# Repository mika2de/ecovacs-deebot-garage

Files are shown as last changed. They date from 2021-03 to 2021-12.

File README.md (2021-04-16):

# Automated robot vacuum cleaner garage

## Description

The robot controlls it all! 100% automation, no manual interactions, invisible installation.

The robot leaves the charging station and operates a mechanical switch that turns on the power. The software opens the door immediately, waits 30 sec to give the robot enough time to leave the garage and then closes the door.

On return it sends an event to the manufactor's server. The software listens to this event, sets the garage into homecoming mode, opens the door and waits for the robot to arrive. A thin force sensing resistor, placed a few centimeteres in front of the charging station, notices when the robot overruns it. That gives the signal to close the garage door right before the power is switched off again.

If the robot didn't return within 5 minutes it is assumed to be trapped and the door gets lowered again. Remove the barriers, say `hey google, return my robot to charging dock` and both robot and garage door execute the homecoming command.

***

## Videos

Robot vacuum cleaner leaves the docking station. 

Automated robot vacuum cleaner garage - start cleaning (https://www.youtube.com/watch?v=2y_Sdoj8P9I "Automated robot vacuum cleaner garage - start cleaning")

The robot returns to the charging station. The ESP received the homecoming event, opened the door and waits for the robot to run over the force resistance sensor.

Automated robot vacuum cleaner garage - returning home (https://www.youtube.com/watch?v=6Qcx_HnqS7c "Automated robot vacuum cleaner garage - returning home")

The kitchen skirting board is heavy, a regular nema 17 cannot lift or hold it. Thus it needs a gearing mechanism. Lucky you if you have a 3D printer at home.

Automated robot vacuum cleaner garage - returning home (https://www.youtube.com/watch?v=Ibu8yQTSDAc "Automated robot vacuum cleaner garage - returning home")

***

## How it works

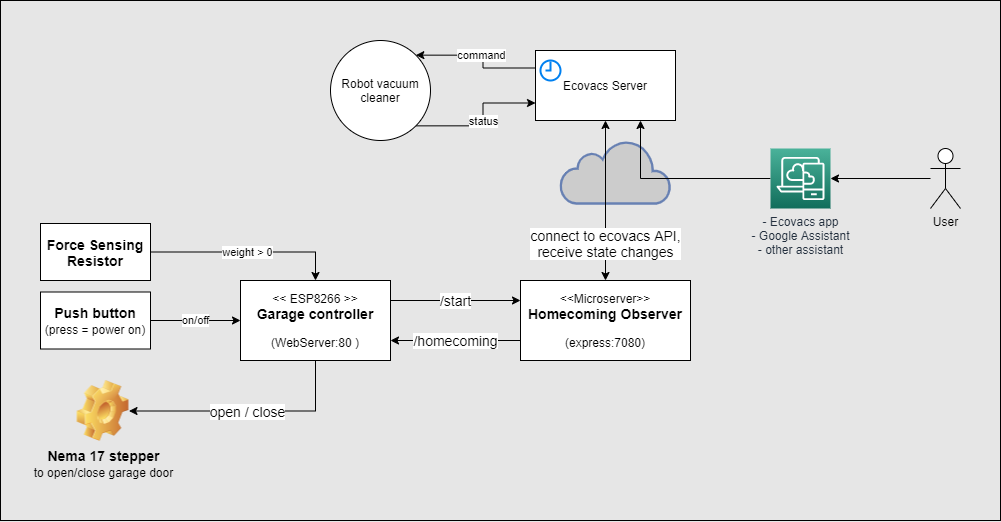
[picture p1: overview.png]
overview


The ESP8266 operates a nema 17 stepper motor that lifts the kitchen skirting board up and down. As long as the robot is in parking postion, one of the robot's wheels stand on an inverted push button so the ESP is powered off. The power is turned on when the robot starts leaving the docking station. On startup the controller executes the following startup routine:

```C++
void setup(){
  Serial.begin(9600);

  // stepper pins
  pinMode(enablePin, OUTPUT);
  pinMode(stepPin, OUTPUT);
  pinMode(dirPin, OUTPUT);

  // force resistance pin
  pinMode(frsPin, INPUT);

  openDoorWaitAndClose(); // function waits 30 sec before closing the door again
 
  // connect to home WiFi
  WiFi.mode(WIFI_STA);
  WiFi.begin(ssid, password);
  Serial.print("Attempting to connect to WPA ");
  Serial.println(ssid);
  if (WiFi.waitForConnectResult() != WL_CONNECTED) {
    Serial.println("WiFi failed!");
    return;
  }
  Serial.println("connected");
  Serial.println(WiFi.localIP());

  // register API endpoints on ESP8266WebServer
  server.on("/open", handleOpenDoor); // for test usage
  server.on("/close", handleCloseDoor); // for test usage
  server.on("/homecoming", handleHomecoming); // for use by nodejs server
  server.onNotFound(handleNotFound); 
  server.begin();
  Serial.println("HTTP server started");

  // send signal to nodejs server
  wakeupBackendService();
}
```
The nodejs server opens a connection to the Ecovacs REST API and starts to listens for inbound status notification events. If the "returning" event is received, the program forwards the event via http to the ESP8266WebServer.

```js
const observe = async () => {
    if (vacbot !== undefined) {
        console.log('Already observing')
        return
    }
    console.log('Start observing')

    const connectStatus = await api.connect(username, passwordHash)
    const devices = await api.devices()
    let vacuum = devices[0];
    vacbot = api.getVacBot(api.uid, EcoVacsAPI.REALM, api.resource, api.user_access_token, vacuum, continent)

    vacbot.on('ready', async (event) => {
        console.log('Vacbot ready')

        vacbot.on('CleanReport', async (state) => {
            console.log('CleanReport: ' + state)

            if (state === 'returning') {
                disconnect()
                vacbot = undefined

                console.log('Try open garage door')
                var response = await openGarage()
                console.log('Garage door opens...')

                let i = 0
                while (response !== 200 && i < 5) {
                    i++;
                    console.log(`Error ${response}, retry open garage door #${i}`)
                    response = await openGarage()
                    await sleep(500)
                }
            }
        })
    })

    process.on('SIGINT', function () {
        console.log("\nGracefully shutting down from SIGINT (Ctrl+C)")
        disconnect()
        process.exit()
    });

    function disconnect() {
        try {
            vacbot.disconnect();
        } catch (e) {
            console.log('Failure disconnecting: ', e.message)
        }
    }
}
```

The ESP is now set into homecoming mode. The homecoming function waits for the robot to run over the force sensing resistor, that is placed right in front of charging station, and closes the door in the final moment before the system is powered off again.

```C++
void homecoming(){
  openDoor();
  do {
    frsValue = analogRead(frsPin);
    delay(500);
  } while (frsValue == 0); // wait for force resistance sensor signal, the quickly close the door before the power is turned off
  closeDoor();
}
```

***

## Build instructions

### NodeMCU, motor and force sensitive resistor wiring

My circuit is run by a single 12V 5A power supply. A  L298N H-Bridge that I had in spare converts 12V in 5V and provides this as input to the ESP8266. This allows me to easily switch on/off the ESP8266 and the stepper driver by a push button. 

In my first experiments I used the L298N to operate the Nema 17 stepper. That wasn't a good idea. I burned my ESP8266 when I performed a physical load test  to figure out how much kilogram the motor (and driver) is able to lift and hold. So I read a bit about stepper drivers other guys use and gave it a try with the A9488 stepper driver. Even under stress it works like a charm, in the worst case the stepper overruns a step.

The A9488 has a on-board potentiometer that one can use to adjust voltage for the motor. Default setting was already good but not sufficient, in my case a quater turn in clockwise direction gave the motor enough power to lift my 1 kg kitchen skirting board.

Don't forget the electrolytic capacitor (100 µF) to protect the stepper driver from spikes.

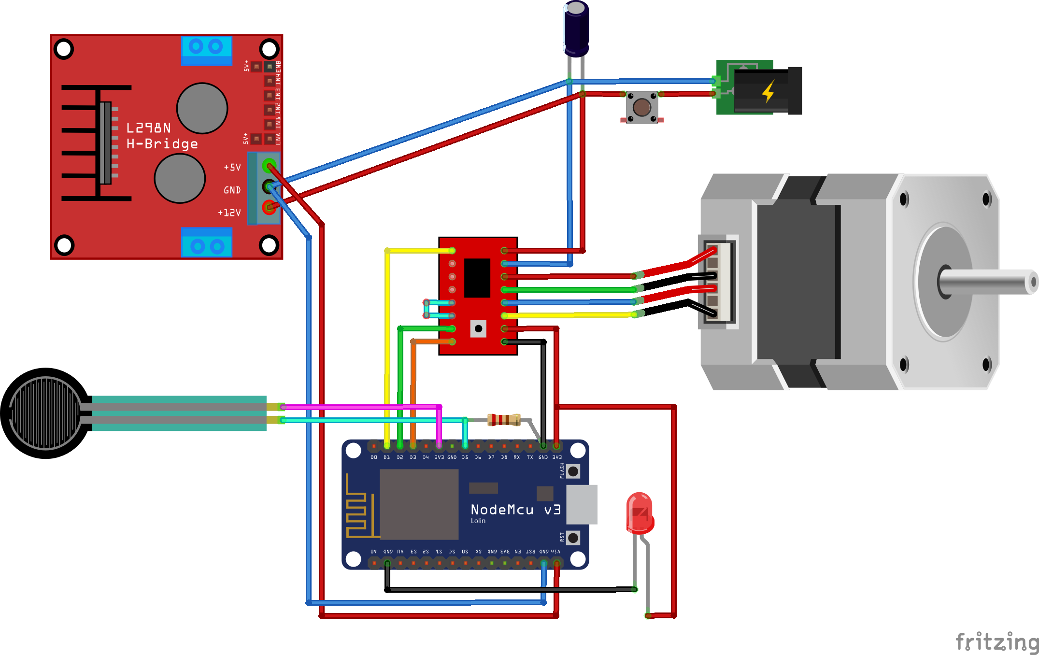
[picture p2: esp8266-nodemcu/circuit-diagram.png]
circuit diagram


### 3D print the reduction gear

For this reduction gear design I finally did my first steps with OpenSCAD. To get accurate gears I used the MCAD/involute_gears.scad library. For my [previous designs](https://www.thingiverse.com/mika2de/designs) I used FreeCAD which was sort of okish for me, but now that I switched to OpenSCAD there is no going back. The reduction gear source file is available in folder cad-models, modify according to your needs. In addition you might find https://geargenerator.com/ helpful, too. 

Reduction gear in OpenSCAD

### Prepare the kitchen skirting board

Check the following image on how to install the hings on your kitchen skirting board. If the hing is not centered like in the middle picture, your skirting board won't hang in a 90° angle from your cupboard. However, when the hinge is centered and you place your skirting board not directly at the front of cupboard but a few centimeters back, you need a pad to open the garage door completely without being blocked by the bottom of the cupboard. 

How to mount the skirting board

Depending on your hinge, you can customize yourself the pad with just a few lines of OpenSCAD code:

```C++
difference() {
    cube([42,11,7]);
    translate([1,0,-0.1]) cube([40,10,1.2]);
    translate([8,5,0]) cylinder(h=20,r=1.5,$fn=20);
    translate([34,5,0]) cylinder(h=20,r=1.5,$fn=20);
}
```

### Run homecoming observer in background

I've a HP microserver running at home, which I reused to host my tiny nodejs homecoming observer program. I installed it in a unix VM and configured it to run after VM startup. 

### Install hardware

Mount the reduction gear to a e.g. wood construction of your choice. If you don't have much space like me, try to position the stepper motor higher at a height that allows the robot vacuum cleaner to drive under it. This gives the robot a bit more space to move. 

parking position image 1

The force sensitive resistor's purpose is to give a signal to the ESP8266 to close the door when the robot is back in the garage. Since the circuit will be powered off as soon as the robot wheel stands on the inverted push button you need to place the FSR needs to be placed a few centimeters in front of the push button. This also depends on the speed of your robot. The slower the robot move towards the charging station, the closer you can put the FSR to the push button. If you put it too close to the button, it could happen that the ESP has not enough time to close the door before it is powered off.

parking position image 1

parking position image 1

## More 

See project log on https://hackaday.io/project/178993-space-saving-automated-robot-vacuum-cleaner-garage

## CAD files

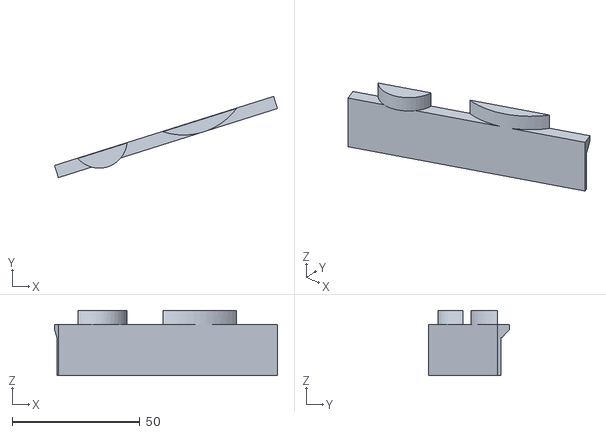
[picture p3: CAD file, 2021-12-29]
cad-models/v2/mount-of-giant-motor-mount.stl
87.3 x 31.8 x 25.5

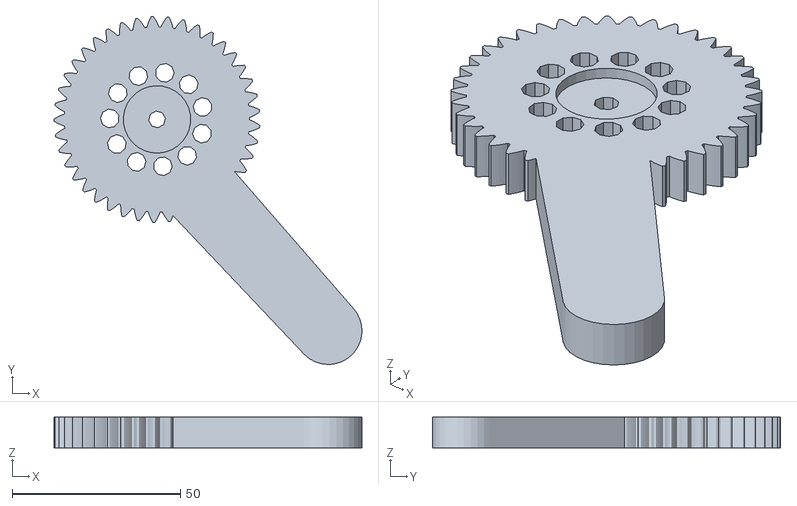
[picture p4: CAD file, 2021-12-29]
cad-models/v2/lift-door-arm.stl
91.4 x 103.3 x 9.20

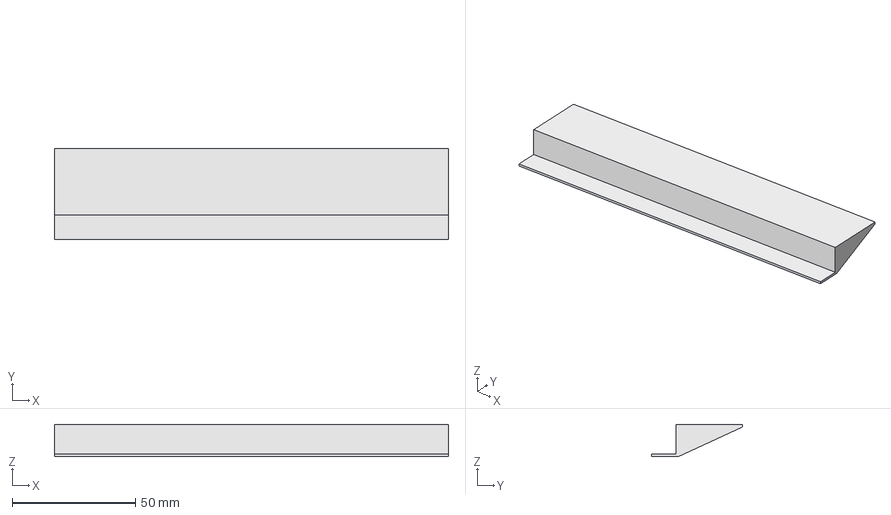
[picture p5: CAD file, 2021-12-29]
cad-models/v2/ramp.FCStd
160.0 x 37.0 x 13.0 mm

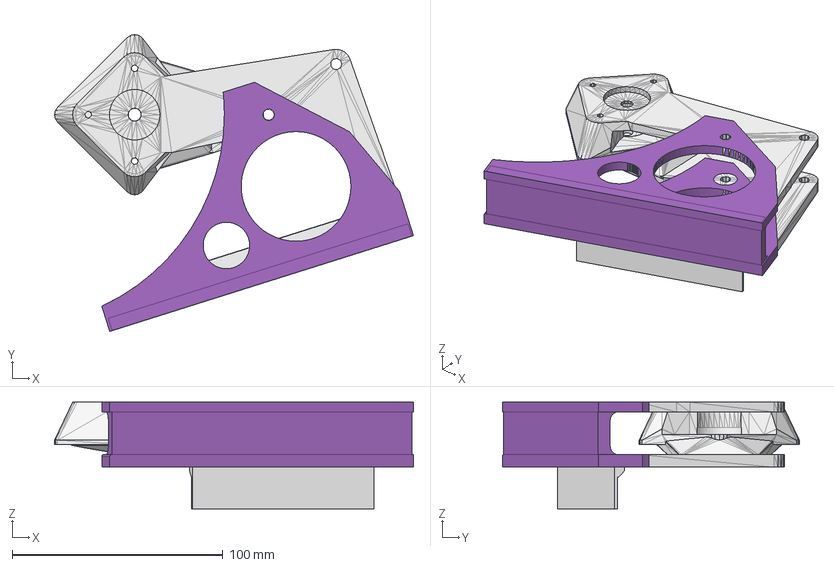
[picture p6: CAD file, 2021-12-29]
cad-models/v2/giant-motor-mount.FCStd
170.2 x 140.7 x 50.5 mm
Würfel003

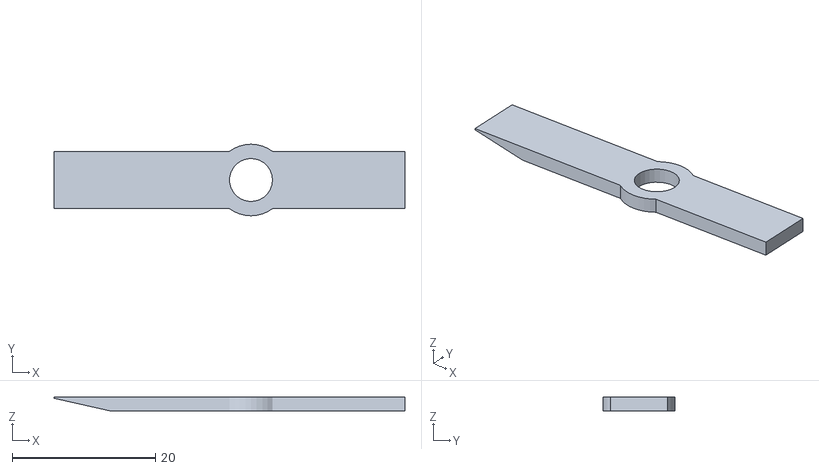
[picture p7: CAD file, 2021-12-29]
cad-models/v2/small-gear-mount.stl
49.0 x 10.0 x 2.00

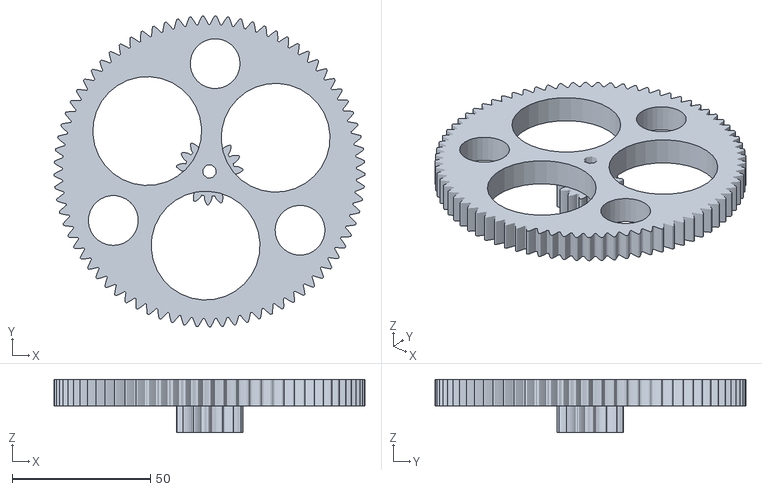
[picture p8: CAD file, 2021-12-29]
cad-models/v2/double-gear.stl
112.3 x 112.3 x 19.2

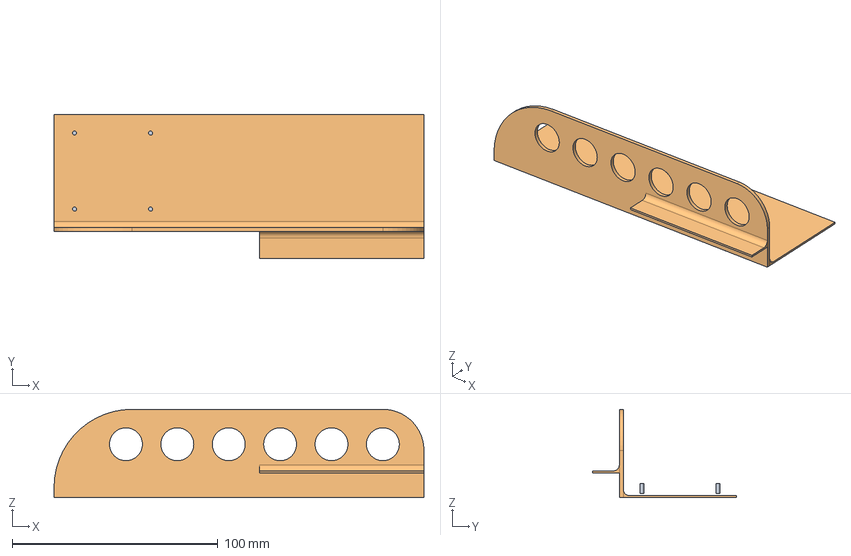
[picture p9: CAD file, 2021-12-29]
cad-models/v2/circuit-plate.FCStd
180.0 x 70.0 x 43.0 mm

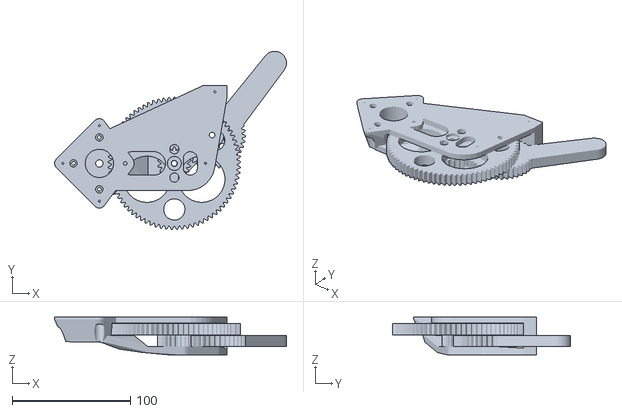
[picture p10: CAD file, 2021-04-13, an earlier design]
cad-models/v1/garage-door/assembling.stl
196.5 x 151.1 x 31.8

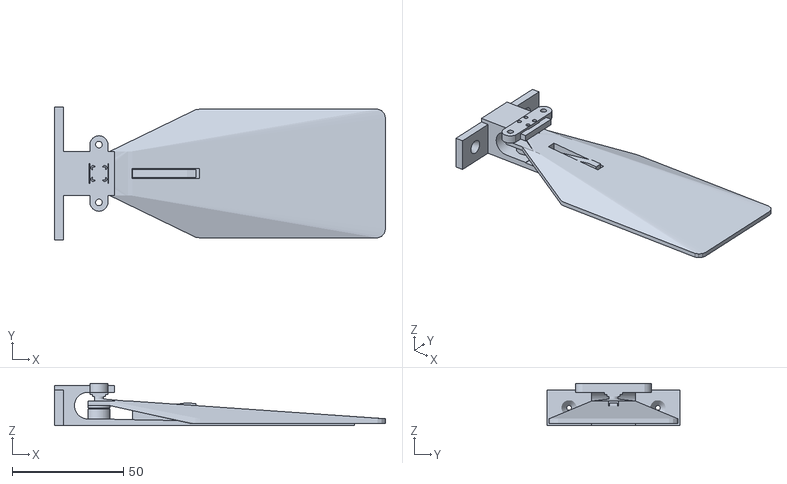
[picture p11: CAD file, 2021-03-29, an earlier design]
cad-models/v1/docking-switch/assembling.stl
149.0 x 60.0 x 19.0

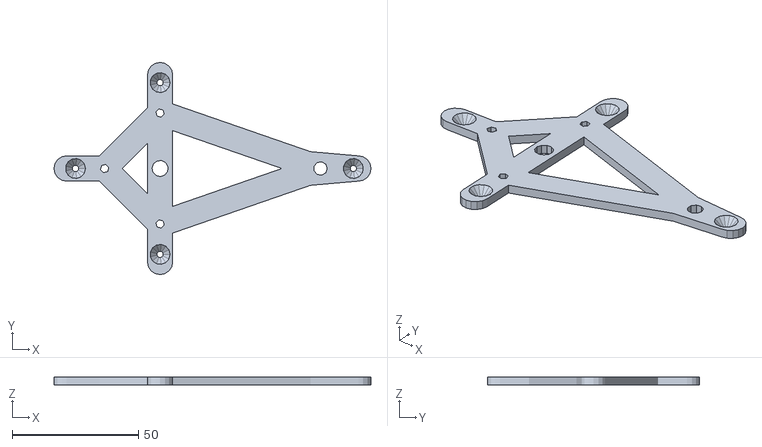
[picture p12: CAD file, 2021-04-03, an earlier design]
cad-models/v1/docking-switch/wall-mount.stl
125.5 x 84.0 x 3.00

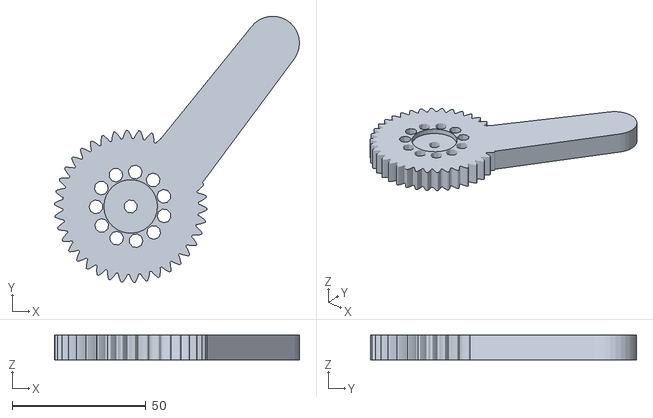
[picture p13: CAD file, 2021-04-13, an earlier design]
cad-models/v1/garage-door/gear-with-arm.stl
91.4 x 99.4 x 9.20

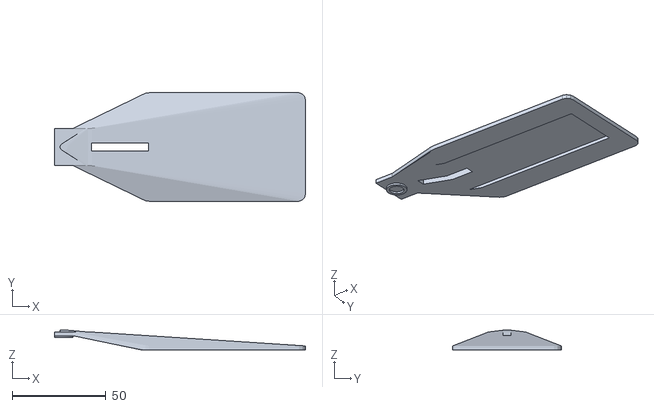
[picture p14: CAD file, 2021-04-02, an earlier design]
cad-models/v1/docking-switch/base-plate.stl
134.0 x 57.9 x 10.5

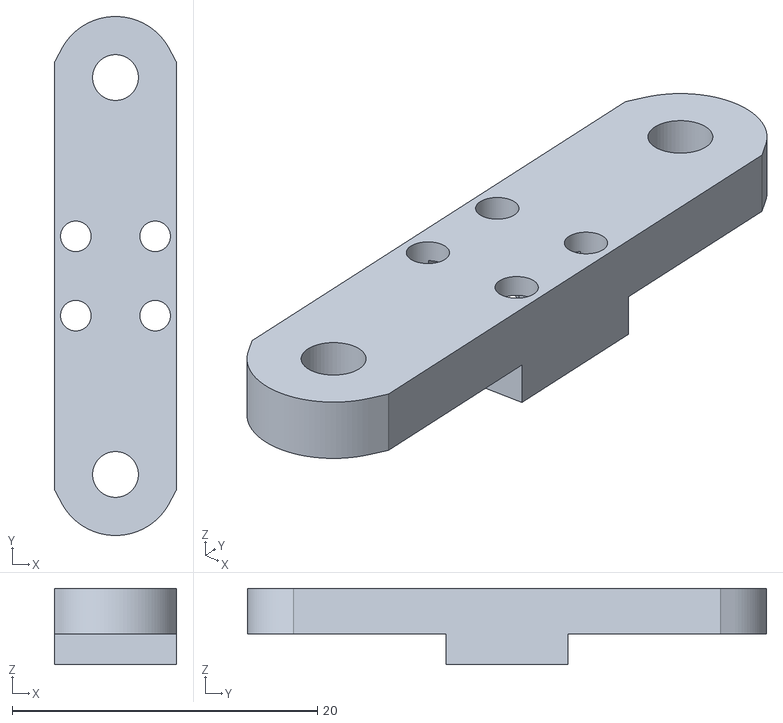
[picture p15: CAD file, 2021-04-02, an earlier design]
cad-models/v1/docking-switch/switch-mount.stl
8.00 x 34.0 x 5.00

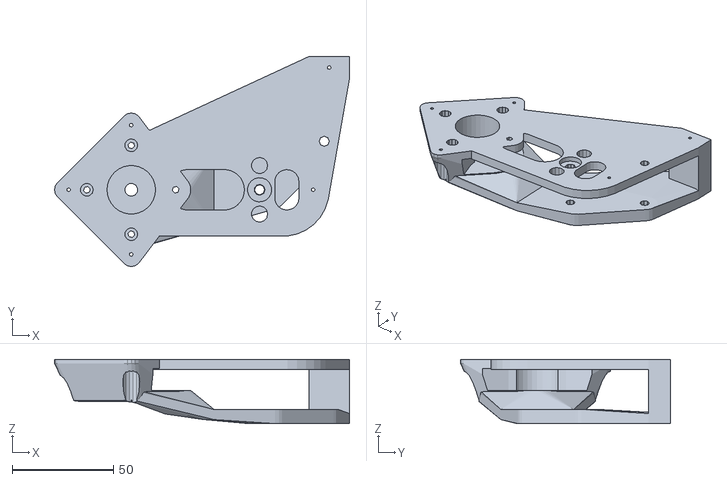
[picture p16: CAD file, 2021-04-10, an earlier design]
cad-models/v1/garage-door/motor-mount.stl
146.0 x 104.0 x 31.8

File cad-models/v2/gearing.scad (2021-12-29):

// DRAFT
// Quick'n dirty cad file used to export the unfinished giantMount.stl which I used as input for FreeCad to finally finish it.

use <MCAD/involute_gears.scad>
include <MCAD/stepper.scad>

tol_x = .2;
tol_z = .4;
gear_thickness=10;

module newGear(teeth, gear_thickness, circle) {
    gear(
        number_of_teeth=teeth,
        circular_pitch=256,
        twist=0,
        rim_width=2,
        rim_thickness=gear_thickness-tol_z,
        hub_diameter=5,
        hub_thickness=gear_thickness-tol_z,
        gear_thickness=gear_thickness-tol_z,
        circles=circle,
        bore_diameter=5
    ); 
}


module liftDoorArm() {
    difference() {
        translate([32,24,-10+tol_z]) rotate([0,0,17]) newGear(41,10-tol_z,11);
        translate([32,24,-3+tol_z]) cylinder(10-tol_z, r=10);
    }
    hull() {
        intersection() {
            translate([32,24,-10+tol_z]) rotate([0,0,-2.5]) newGear(38,10-tol_z,5);
            translate([55,45,-10+tol_z]) cylinder(10-tol_z, r=13);
        }
        translate([85,85,-10+tol_z]) cylinder(10-2*tol_z, r=10);
    }

}

module doubeGear() {
    color("LightBlue") difference() {
        newGear(77,10,3);
        for(n = [1 : 3])
                rotate([0, 0, 60 + n * 120])
        {
            translate([39,0,0])
            cylinder(50, r=9);
        }
    }
    
    translate([0,0,-10+tol_z]) color("LightYellow") newGear(15,10,7);
    //rotate([0,0,-90]) liftDoorArm();

}

module small_gear(teeth) {
    color([0,0,1]) translate([-2.5,1.9,0]) cube([5,2,15-tol_z]);
    gear(
        number_of_teeth=teeth,
        circular_pitch=256,
        twist=0,
        rim_width=2,
        rim_thickness=gear_thickness,
        hub_diameter=10,
        hub_thickness=15-tol_z,
        bore_diameter=5+4*tol_x,
        gear_thickness=gear_thickness-1,
        circles=5
    );
}

module nema() {
    motor(Nema17, NemaShort);
}

module nema17_hole(depth=10) {
    linear_extrude(depth) minkowski() {
        circle(6);
        square([31.04, 31.04], true);
    }
    translate([0, 0, -depth])
    cylinder(depth+1, r=3+tol_x);
    for (i = [0:3]) {
        rotate([0, 0, i*90])
        translate([31.04/2, 31.04/2, -depth])
        cylinder(depth+1, r=1.5+tol_x);
    }
}

module giantMount() {
    translate([-15.5,0,10]) rotate([180,0,0]) difference() {
        union() {
            difference() {
                translate([-48, 0, -5]) union() {
                    hull() {
                        linear_extrude(20) minkowski() {
                            circle(7.48);
                            rotate([0,0,45]) square([31.04, 31.04], true);
                        }
                        translate([0, 33, 18]) cylinder(2, r=5);
                        translate([0, -33, 18]) cylinder(2, r=5);
                        translate([-33, 0, 18]) cylinder(2, r=5);
                    }
                }            
                // big gear cut
                translate([25, 0, -tol_z]) cylinder(10+2*tol_z, r=68); 
            
            
            // top hole for small gear 
            translate([-48, 0, -tol_z]) cylinder(20, r=12);
        
            // motor screw holes
            translate([-48, 0, -5]) rotate([0,0,45]) mirror([0, 0, 1]) nema17_hole(20);
        
            // motor knop hole        
            translate([-48, 0, -5]) cylinder(3.2, r=12);
        
            // countersinks motor
            translate([-48, 22, 9.2]) cylinder(20,r=3.2);
            translate([-48, -22, 9.2]) cylinder(20,r=3.2);
            translate([-70, 0, 9.2]) cylinder(20,r=3.2);
        }
        
translate([00, -0, -24.4]) union() {
        translate([20, -0, 9]) hull() { 
            translate([50, 40, 10.4]) cylinder(4.6, r=7);    
            translate([0, 0, 10.4]) cylinder(4.6, r=7);  
            translate([27.5, -24, 10.4]) cylinder(4.6, r=7); 

        }
        translate([20, -0, 9]) hull() { 
            translate([-40-15.5, -18, 10.4]) cube([5,36,4.6]);
            translate([0, 0, 10.4]) cylinder(4.6, r=7);  
            translate([27.5, -24, 10.4]) cylinder(4.6, r=7); 
        }
    }
        translate([-50.5,0,10.4]) hull() {
            linear_extrude(5) minkowski() {
                circle(7.48);
                rotate([0,0,45]) square([31.04, 31.04], true);
            }
            translate([35, -18, 10.4]) cube([5,36,5]);
        }
        union() {
        translate([20, -0, 9.4]) hull() { 
            translate([50, 40, 10.4]) cylinder(6, r=7);    
            translate([0, 0, 10.4]) cylinder(6, r=7);  
            translate([27.5, -24, 10.4]) cylinder(6, r=7); 

        }
        translate([20, -0, 9.4]) hull() { 
            translate([-20-15.5, -18, 10.4]) cube([5,36,6]);
            translate([0, 0, 10.4]) cylinder(6, r=7);  
            translate([27.5, -24, 10.4]) cylinder(6, r=7); 
        }
    }
        translate([70, 40, -2]) cylinder(27, r=7); 
    translate([110.5-42, 14, 10.4-10-5.4]) rotate([0,0,72.5]) cube([46,84,4.6]);

    }
    
    translate([15.5,0,-10]) union() {
            //translate([13, 0, 16]) cylinder(4.1,0.3,4,true);
        //translate([-97, 0, 16]) cylinder(4.1,0.3,4,true);
        //translate([-63.5, 34, 16]) cylinder(4.1,0.3,4,true);
        //translate([-63.5, -34, 16]) cylinder(4.1,0.3,4,true);
        translate([0, 0, -40]) cylinder(100, r=2.5+tol_x);
    }
}

}


rotate([0,0,27]) doubeGear(); 
//translate([-63.5,0,0]) rotate([0,0,$t*90+3.8]) small_gear(12);
//translate([0,0,-40]) 
//color("LightCyan") translate([14,59.7,0]) rotate([0,0,-100]) liftDoorArm();

// translate([-48-15.5, 0, -5-25]) rotate([0,0,45]) mirror([0, 0, 1]) nema();
//translate([-48-15.5, 0, 14.5]) rotate([180,0,45]) mirror([0, 0, 1]) nema();
// difference() {giantMount();
//translate([32, 24, -40]) cylinder(100, r=2.5+tol_x);}

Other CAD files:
cad-models/v1/docking-switch/base.stl
cad-models/v1/garage-door/hinge-socle.stl
cad-models/v1/garage-door/middle-gears.stl
cad-models/v1/garage-door/small-gear.stl
cad-models/v1/docking-switch/power-off-switch.scad
cad-models/v1/garage-door/gearing.scad
cad-models/v1/garage-door/hinge-socle.scad
cad-models/v2/circuit-plate.stl
cad-models/v2/giant-motor-mount.stl
cad-models/v2/ramp.stl

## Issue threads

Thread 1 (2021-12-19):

Unreliable parking process

mika2de, 2021-12-19:
As a result of the limited space under the kitchen cupboard, the Ecovacs Deboot occasionally has difficulties returning to the docking station. The robot gets stuck on the cabinet feet foot plate. The parking process then cancels after a few minutes.

To solve the problem, the door lifting mechanism must be partially redesigned in order to leave more space for the robot. In addition by raising the floor (of the lane to the docking station) to the level of the foot plate, the robot can drive over it so that 4 cm of more space can be gained.

Closed 2021-12-29.

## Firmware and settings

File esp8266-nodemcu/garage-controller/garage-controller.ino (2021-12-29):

#include "ESP8266WiFi.h"
#include "ESP8266HTTPClient.h"
#include "AccelStepper.h"
#include <ESP8266WebServer.h> 

// WiFi and http server
const char* ssid = "MY_SSID";
const char* password =  "MY_WIFI_PASSWORD";
ESP8266WebServer server(80);

// Nodejs backend
const String host = "MY_NODEJS_BACKEND_SERVICE_IP";
const int port = 7080;
const String url = "/start";
WiFiClient client;

// Stepper motor
const int enablePin = D1;
const int stepPin = D2;
const int dirPin = D3;
const int openCloseSteps = 740; // steps to go from position 0 to open the door
AccelStepper stepper = AccelStepper(AccelStepper::DRIVER, stepPin, dirPin);

// force resistance sensor
const int frsPin = D5;
float frsValue;
 
void setup(){
  Serial.begin(9600);

  // stepper pins
  pinMode(enablePin, OUTPUT);
  pinMode(stepPin, OUTPUT);
  pinMode(dirPin, OUTPUT);

  pinMode(frsPin, INPUT);

  openDoorWaitAndClose();
 
  WiFi.mode(WIFI_STA);
  WiFi.begin(ssid, password);
  Serial.print("Attempting to connect to WPA ");
  Serial.println(ssid);
  if (WiFi.waitForConnectResult() != WL_CONNECTED) {
    Serial.println("WiFi connection attempt failed");
    delay(10000); // wait 10 sec
    WiFi.begin(ssid, password);
    Serial.println("2nd attempt...");
    if (WiFi.waitForConnectResult() != WL_CONNECTED) {
      Serial.println("2nd attempt failed");
      delay(60000); // wait 60 sec
      WiFi.begin(ssid, password);
      Serial.println("3rd attempt...");
      if (WiFi.waitForConnectResult() != WL_CONNECTED) {
        Serial.println("3rd attempt failed");
        return;
      }
    }
  }
  Serial.println("WiFi connected");
 
  Serial.println(WiFi.localIP());

  server.on("/open", handleOpenDoor);
  server.on("/close", handleCloseDoor);
  server.on("/homecoming", handleHomecoming);
  server.onNotFound(handleNotFound); 
  server.begin();
  Serial.println("HTTP server started");

  wakeupBackendService();
}
 
void loop(){
  server.handleClient();
}

void handleOpenDoor(){
  server.send(200, "text/plain", "open door");
  openDoor();
}

void handleCloseDoor(){
  server.send(200, "text/plain", "close door");
  closeDoor();
}

void handleHomecoming(){
  server.send(200, "text/plain", "enter homecoming mode");
  homecoming();
}

void handleNotFound(){
  server.send(404, "text/plain", "404: oh snap");
}

void homecoming(){
  openDoor();
  int counter = 0;
  do {
    counter++;
    frsValue = analogRead(frsPin);
    delay(500);
  } while (frsValue == 0 && counter <= 600); // wait for force resistance sensor signal, the quickly close the door before the power is turned off. Close door if robot wasn't able to return after 5min.
  closeDoor();
}

void openDoor() {
  Serial.println("open");
  digitalWrite(enablePin, LOW); // enables a4988
  stepper.setMaxSpeed(1000.0);
  stepper.setAcceleration(2500.0);
  stepper.moveTo(openCloseSteps);
  stepper.runToPosition();
  // do not disable stepper, hold the door!
}

void closeDoor() {
  Serial.println("close");
  digitalWrite(enablePin, LOW); // enables a4988
  stepper.setSpeed(-1000.0);
  stepper.moveTo(0);
  stepper.runToPosition();
  digitalWrite(enablePin, HIGH); // disables a4988
}

void openDoorWaitAndClose() {
  openDoor();
  delay(30000); // wait 30 sec. for robot to leave parking position
  
  closeDoor();
}

int wakeupBackendService() {
  HTTPClient http;
  http.begin("http://"+host+":"+port+"/start");
  int httpCode = http.GET(); // send request
 
  if (httpCode > 0) {
    String payload = http.getString();
    Serial.println(payload);
  } else {
    Serial.println("error. " + httpCode);
  }
  http.end(); // close connection
}

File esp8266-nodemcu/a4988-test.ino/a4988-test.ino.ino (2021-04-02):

// Define pin connections & motor's steps per revolution
const int enablePin = D1;
const int stepPin = D2;
const int dirPin = D3;
const int openCloseSteps = 340;

void setup()
{
  // Declare pins as Outputs
  pinMode(enablePin, OUTPUT);
  pinMode(stepPin, OUTPUT);
  pinMode(dirPin, OUTPUT);

  digitalWrite(enablePin, LOW
  );
  Serial.begin(9600);
}
void loop()
{
  // open door
  digitalWrite(dirPin, LOW);

  // Spin motor slowly
  Serial.println("open");
  for(int x = 0; x < openCloseSteps; x++)
  {
    digitalWrite(stepPin, HIGH);
    delayMicroseconds(1000);
    digitalWrite(stepPin, LOW);
    delayMicroseconds(1000);
    yield();
  }
  delay(1000); // Wait a second
  
  // close door
  digitalWrite(dirPin, HIGH);

  // Spin motor quickly
  Serial.println("close");
  for(int x = 0; x < openCloseSteps; x++)
  {
    digitalWrite(stepPin, HIGH);
    delayMicroseconds(1000);
    digitalWrite(stepPin, LOW);
    delayMicroseconds(1000);
    yield();
  }
  delay(1000); // Wait a second
}

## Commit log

2021-03-25 circuit diagram without push button
    [circuit-diagram.fzz]
2021-03-25 customized gearing scad
    [gearing.scad]
2021-03-25 WIP gearing
    [gearing.scad]
2021-03-26 added arm to big gear
    [gearing-with-arm.stl, gearing.scad]
2021-03-26 circuit diagram and motor mount
    [circuit-diagram.fzz, gearing.scad, motor-mount.stl]
2021-03-28 updated gearing
    [assembling.stl, gearing-with-arm.stl, gearing.scad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]
2021-03-28 added base switch model
    [assembling.stl, base-plate.stl, base.stl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]
2021-03-29 refined base and base-plate
    [assembling.stl, base-plate.stl, base.stl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]
2021-04-02 stepper motor using a4988
    [base-plate.stl, gearing.scad, motor-mount.stl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]
2021-04-03 new lever moved to upper left corner, using 4 gears
    [assembling.stl, gear-with-arm.stl, gearing-with-arm.stl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]
2021-04-04 close door using force resistance sensor
2021-04-05 shortend lifting arm
    [assembling.stl, gear-with-arm.stl, gearing.scad]
2021-04-06 resized gears for higher torgue
    [assembling.stl, gear-with-arm.stl, gearing.scad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]
2021-04-07 migrate to ESP8266WebServer to fix yield bug
    [garage-controller.ino]
2021-04-07 reworked gearing to achieve higher torque
    [gear-with-arm.stl, gearing.scad, middle-gears.stl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]
2021-04-07 for now final gearing
    [assembling.stl, gearing.scad]
2021-04-09 hinge socle to not jolt open door with cupboard bottom
    [hinge-socle.scad, hinge-socle.stl]
2021-04-10 final fixes before hardware installation
    [circuit-diagram.fzz, gearing.scad, hinge-socle.scad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]
2021-04-10 stronger gearing mount
    [assembling.stl]
2021-04-11 updated diagrams
    [circuit-diagram.fzz]
2021-04-13 stabilized reduction gear mount, update readme
    [assembling.stl, gear-with-arm.stl, gearing.scad]
2021-12-19 WIP - redesign motor mount
    [gearing.scad]
2021-12-22 v2 mechanic redesign
    [assembling.stl, base-plate.stl, base.stl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]
2021-12-29 plugable motor mount
    [gearing.scad, giant-motor-mount.FCStd, mount-of-giant-motor-mount.stl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]
